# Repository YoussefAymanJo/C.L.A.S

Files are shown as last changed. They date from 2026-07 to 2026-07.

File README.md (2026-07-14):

# C.L.A.S

## Description
Is an abbreviation for a closed-loop feedback system.A system that monitors and acts based on lettuce & pepper plant conditions in 6th October city,Egypt.
In  monitors temperature & Humidty & soil moiture & light intensity.then,it responds in case in change in plants optimal range conditonns.As,it used actuctors,peltiers ,humidifier,heating lamp ,grow light , water pump and fan to out excessive humidty.It powered by esp s3.and cloud base storage of firebase,show data at moment on web app.
## Why it was built
This is grade 11 Capstone Project in my school,so i must make it.It is about the challenge Egypt faces in integrating IoT closed systems with farming.My project solve this by providing high nutrition needed crops in my area all the year,lettuce&pepper controlled  by closed feedback system.that control temperature & humidty & soil moisture & light parameters.
## How to use it / Build it
 First of all,prepare materials ,then buy wood and start cut into blocks,after that open parts in wood using cnc for actuactors and other in pcb enclosure.After that assemble all together using nails and wood glue.then adding electronic compontes sesnor & actucators.and connect them first to power supply to test it.then connect each one alone first to esp ,then test them all.after that,check wire isolation and system working and real data from sesnors.test system manul for 2 h. Finally, add plants and soil.
## Schematic
I made symbols & footprints for missing parts in kicad,then wires them ,and add pin headers instead of wire sensor direct to pcb,finally,organize schematic and adding flow diagram of system feedback.


## PCB
pcb consist of pinheaders and will connect to sensors using isolated wires & jumpers,and actuctors will connect to mosfets.I made pcb on kicad,body outline first,the routed componets together.


## CAD
i assembled greenhouse on fusion and make enclosure for pcb ,power supply & buck.



## Firmware
I made esp code and web to monitor data form firebase,but i will add js part later during building
### ESp code 

### website 
https://youssefaymanjo.github.io/WEb-clas/
## BOM 
I made the BOM  and needed materials ,in egypt then convert its price to USD dollar.


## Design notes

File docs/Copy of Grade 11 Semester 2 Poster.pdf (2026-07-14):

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
Aref | C.L.A.S Marwan Ahmed

# Youssef Ayman

10205
Abstract | Conclusions Grade 11 2025-2026

# 1st Semester STEM High School for Boys - 6th of October

# Introduction

Egypt struggles with some harsh challenges that hinders its development towards the vision of 2030. Through this vision, Egypt was facing tough problems that may stops the progress of the 2030 vision. One of these problems is the pollution of air, water, and soil, damaging the crops and the crop land. Egypt generates over 100 million tons of solid waste annually including Municipal solid waste, Construction and demolition waste,and Industrial and agricultural waste. Also, Egypt produces 16.4 billion cubic meters of wastewater annually including agricultural sources, and sewage. The health of the soil in the Nile Delta region is declining due to the growing number of enterprises and their emissions, urbanization, increased congestion, and the utilization of sewage and waste sediments. Although the Nile Delta covers only 20,000 km2, it accounts for 46% of Egypt’s total agricultural area, which is 55,040 km2

Image | Name | Quantity | Description
| Recycled wooden box | 1 box | A recycled wooden box to contain all the components in it.
| Polyethylene Film | ~ 2 meter-squared | A single layer film used to wrap the prototype to prevent heat leakage.
Relay module | 2 4-channel 1 2-channel

A module which turns on/off the actuators based on a signal from the ESP32.

ESP-32S 38Pin | 1 Dev board | The motherboard of the whole prototype, it is responsible for managing all the parts and the signals passing through.
Peltier | 2 Peltiers | Are devices responsible for generating heat flux by passing electric current to the both sides.
DC Fan | 5 Fans | Are significant for venetrating the prototype parts.
Growth Light | ~ 1 meter | Used to give light to the plant that is responsible for its growth.

Soil moisture and irrigation growth model
Soil moisture is an essential topic in green farming, as it indicates when the plants need to be watered. Studies indicate that soil temperature and moisture are strongly interconnected and directly influence plant root growth and water movement. Additionally, higher soil temperature increases evaporation, accelerating moisture loss. However, the soil moisture sensor does not give a true percentage from the beginning; it needs more calculations following Equation 2

# Literature Cited

Ventilation and roofing impacts on temperature
The greenhouse roof traps heat, increasing internal temperature. Ventilation reduces this heat by allowing air exchange between the inside and outside environments.
Learning Outcome | Concept | Content | Relation
CS.2.06 | 1 | User interface

Helps to understand how
to design and manage
System using App
interface
BI2.09 | 2 to 4 | Hormone Cycle | Helps us to understand how closed feedback system operates
ES.2.09 | 1 to 6 | Earth Cycle | Helps us to understand how closed feedback system operates
PH.2.09 | 1 to 6 | Circuit and charge and discharge | Helps us to understand how closed feedback system operates
PH.2.10 | 1 to 4 | Ac & Dc generator | Helps us to understand how closed feedback system operates
ME.2.05 | 1 | power | Helps us to understand how closed feedback system operates

Light intensity and photosynthesis efficiency
Light intensity is one of the essential factors controlling photosynthesis in a greenhouse. Solar radiation gives the energy required for converting carbon dioxide and water into glucose, directly affecting plant growth and productivity.
Studies indicate that photosynthetic activity is strongly dependent on incident radiation, especially in controlled environments such as greenhouses, where light availability can limit or enhance crop performance. The factors that affect light intensity are distance, following Equation 3.

I is the light intensity, p is the power of the light source, and d is the distance from the light source. As the plant was moved closer to the grow light by increasing the height, since the distance is squared in the law, the intensity increases quadratically. Increasing light intensity causes an increase in the photosynthesis rate of the plant, following Equation 4.

P(I) is the photosynthetic rate and P_max is the maximum photosynthetic rate k is the half-saturation constant; with this law, it can be concluded that at high light intensity (P)≈P_max

Added all the parts via schematic connection to ensure it is working correctly, as shown in Figure 3.

Implemented the circuit and the rest of the parts of the prototype like the lettuce plant, as shown in Figure 7.

Test Plan
Test plan The objective of this test plan is to evaluate
the validate the prototype and design requirements, focusing on two key aspects, design and mechanism. Parameters testing
The prototype must be able to measure at least 3 parameters properly, in this case, temperature, soil moisture, and humidity were included in our prototype as parameters.
accuracy
To ensure that the device has good accuracy, the temperature, soil moisture, and humidity are measured using the prototype from the STEM High School for Boys - 6 of October school to make sure it met the design requirements within the selected location.

th

Studies indicate that soil temperature and moisture are strongly interconnected and directly influence plant root growth and water movement (Xu Zhang et al., 2025). As soil temperature increases, the thermal energy within the soil rises, enhancing evaporation rates from the surface. At the same time, higher temperatures
stimulate root metabolic activity, increasing water uptake by
plants. As shown in Figure 13, the humidity data collection of
tshaeme greenhouse as it was between 50-52% and 90% as it used the fan and the roofing ventilation system in the first graph showing the temp by percentage The combined effect of increased evaporation and root absorption leads to a faster depletion of soil moisture, particularly in greenhouse environments where heat accumulation is significant. The ventilation system contained a 12V fan for ventilation, as decided following Equation 5.
Q is the total heat lost, and m is the airflow rate, and is the difference between T inside and T out. Indicating that the heat lost with the ventilation system depends on the strength of the fan used

This is critical for Lettuce and Capsicum annuum, since excessive heat can cause stress and reduce productivity. Moreover, the lettuce needs a temperature between 60 () which can be hard to maintain in the summer due to the temperature. The temperature affects the transpiration rate of the plant as well,following Equation 1.
As E is the transpiration rate of the plant and T is the temperature, in other words, the higher the temperature, the greater the loss of water in the plant that the system must maintain.

Calibrated the sensors used for the prototype to make sure it is accurate.

Figure4: Recycled wooden crate

Wrapped the body with a single layer of polyethylene to prevent the leakage of heat from the greenhouse, as shown in Figure 7.

# Acknowledgement

# Materials & Methods

# Results

# Analysis

# Recommendation

Closed | loop
a | GRICULTURAL SYSTEM.

Figure 14: Real-Life Location

# Keywords: Agriculture, lettuce, Feedback System, database

The previous challenges Cause bad consequences, the climate change and the rapid increase in the greenhouse gases in the atmosphere. The climate change occurs because of the burning of the fossil fuels like petroleum. In the last decades, It was observed that the carbon dioxide emissions
in Egypt increased to be 258.37 million ton annually as
shown in the Figure 1.
Two prior solutions were introduced to address the problem. The first was the automated scale aquaponic system, designed for serve the aquatic life by controlling the fish growth in a neutral environment conditions. Smart agricultural solution to autonmous greenhouse control was the second chosen prior solution. It is designed to control the quantity of air in the vaccum, light, and heat inside the prototype.
During the prototype development process, design requirements were chosen to ensure that the prototype would be effective, eco-friendly, safe, accurate, an precise. The chosen solution was a closed-loop agricultural system for suitable for planting lettuce and pepper. It was selected to be implemented in STEM High School for Boys – 6th of October as a location.

Solar Photovoltaic Panels Integration
A highly promising direction in the future development of the project is to integrate a solar photovoltaic panel with energy buffer units in the project to ensure energy continuity. A solar photovoltaic panel is a device that converts the sunlight into electric energy as shown in Figure 15, will be coupled with a buffer unit which acts as an energy storage that is settled between the solar panel and the site of the electrical load. When the panels collect the sunlight and convert it into current, this current will be used in

Figure 15: an image for the solar photo-voltaic cells

Real-Life Location
Boarding schools face multiple difficulties regarding funds. There has been a rapid increase in services and products, which makes it a necessity for schools to find an alternative. As shown in Figure 14, it is highly recommended to make a real-life application of the project in STEM High School for Boys – 6th of October as the location for the implementation of our device's application.
At present, our school depends on external suppliers and delivery
services which increase the costs on the school's financial
manager, increasing the funds that the school apply for. This adds
more pressure on it to cover all the students' demands during their learning journey. This solution will help the school to save on the delivery and ship the food that comes to the students every day by using the project to produce its own demand from fruits and vegetables without needing any shipping which cases a lot. Giving all the students their specified portions of food without any decrease in its amount.

Where θ is the soil moisture by percentage, and the R_dry is the reading of the sensor as the soil is fully dry and R_wet Is the reading when the soil is fully moist

with water, and R current is the reading of the sensor when the soil is in its current state.

Equation 2: Relation between energy and temperature

For Egypt's development towards the future, 2030 vision must be achieved by solving its grand challenges. In this project, two grand challenges was addressed and aimed to be solved, the pollution of air, water, an soil, and the low number of agricultural and industrial bases in Egypt. These grand challenges are aimed to be solved by Egypt to not hinder its economy and development. The project is designed to be implemented in STEM High School for Boys – 6th of October as a real life location as it will help in the problem of high cost of food due to the increase in the cost of the fuel by providing a local source of food for the students. Its simple design and mechanism, ability to be held by the user, and the ability to fit at any environment are from its pros. The project is composed of recycled wooden box as an external structure surrounded by a layer of polyethylene, a tray for holding the soil, lettuce plant, ESP32 as a brain for the circuit, power supply to feed the prototype with electricity, sensors for measuring the temperature, soil moisture, humidity, light intensity as parameters. The project met the design requirements as it contains recycled parts, composed of three parameters with their actuators to stabilize the surrounding environment.

Ten essential materials were used in constructing the prototype, As shown in Table 1 | Negative Results At first, we brought a stepdown converter to decrease the circiut’s voltage and increase the current, but we found that the stepdown was damaged before it was used. This made us took more time than expected to complete the circuit. Secondly, The power supply that was bought to operate the prototype was 12V and 10A. That was a problem because most of the parts in the circuit needed 7A or more, so this made a significant problem on how to operate all the part with the same power supply. To solve this problem, the components were distributed to the power supply’s pins of 10A each to fit all the components.

In conclusion, many grand challenges that hinders its development and its 2030 vision, two main challenges was aimed and addressed by the capstone project, the pollution of air, water, and soil, and the lack in the agricultural and industrial bases. This project aims to solve these problems by providing a solution which is the closed-loop agricultural system, controlling the environmental parameters to make the environmental condition stable. The prototype was build from recycled materials, except the electronic components. It was chosen to integrate the project in STEM High School for Boys – 6th of October as a real-life location, solving the problem of high budget for buying and delivering the food to the students by integrate the prototype in the school to produce its own food, saving its budget.

Methods
Made the 3D design using onshape CAD software to make sure the dimensions are accurate, as shown in Figure 2.

Collected a recycled wooden crate as a body for the prototype, and bought all the electronic parts to build the circuit, as shown in Figure 4.
Build the prototype body using some old wooden parts and the recycled wooden crate by cutting the wood into pieces then sticking them to make the roof of the greenhouse body, as shown in Figure 5.
Added the water container, tray, soil to the greenhouse body as a basic structure, as shown in Figure 6.

Followed the schematic and connected the circuits components correctly, making sure it will work properly.

Polycarbonate Implementation
It is also highly recommended to implement polycarbonate sheets instead of polyethylene single layer sheets as shown in Figure 16, as it will help in developing and improving the prototype efficiency. Polycarbonate is a high-performance, transparent thermoplastic known for its exceptional durability, light weight, and excellent optical clarity. These properties make it one of the
most widely used alternatives to glass in both architectural and
industrial applications. There are many differences between the
polycarbonate and polyethylene sheets, making it more favourable to be implemented in the real-life project, such as High impact resistance, Superior thermal insulation, Excellent light transmission, Built-in UV protection, Long lifespan (10–25 years), and Reduces energy and heating costs. It is not implemented in our prototype because, it costs more than expected to fund it.

Ritchie, H., & Rosado, P. (2025, December 19). CO₂ and Greenhouse Gas Emissions. Our World in Data. https://ourworldindata.org/profile/co2/egypt

Figure 1: CO₂ and Greenhouse Gas Emissions

Figure3: Schematic connections for the prototype using kicad

Figure 7: Greeenhouse prototype after circuit implementation and polyethylene wrapping

Figure 6: Greeenhouse prototype after circuit implementation

Figure 5: Greeenhouse prototype after circuit implementation

Figure 16: an image for the polycarbonate sheets

Figure 13: greenhouse humidity data collection

Temperature effects on the greenhouse
Temperature is a key factor affecting plant growth, evaporation, and transpiration. In greenhouse systems, solar radiation enters through the transparent covering and is partially trapped, increasing the internal temperature. Research shows that evapotranspiration is one of the most crucial processes controlling water movement in greenhouse crops. As temperature increases, the kinetic energy of water molecules and plant physiological activity also increases, leading to higher transpiration rates and accelerated water loss from .

Figure2: 3D design for the prototype the root zone This process is further intensified by increased vapor pressure deficit between the leaf surface and the surrounding air, which enhances the diffusion of water vapor from the plant o the atmosphere. As shown in Figure 12, the data collection of the air temperature from the same study mentioned before. The data shows the air temperature over two months, with fractures as the temperature decreases at night and increases during the day, with an average of 22.5 .(Sustain. Food Syst,2023).

Figure 12: Greenhouse body after adding tray, and cooling system

Positive Results
A reliable closed-loop agricultural system was developed for use in STEM High School for Boys - 6 of October, conforming to the required design requirement, showing the responses from the actuators to the changes in the environment of the project relative to the time taken, and another one showing the environmental parameters changing by passing time.

th

Table3: Learning outcomes used

Equation 3: Relation between light intensity and distance from the light source Equation 4: Relation between photosynthesis rate and light intensity Equation 5: Relation between total heat lost and the air flow rate

Boulard, T., & Wang, S. (2000a). Greenhouse crop transpiration simulation from external climate conditions. Agricultural and Forest Meteorology, 100(1), 25–34. https://doi.org/10.1016/s0168-1923(99)00082-9
Ghiat, I., Govindan, R., & Al-Ansari, T. (2023). Evaluation of evapotranspiration models for cucumbers grown under CO2 enriched and HVAC driven greenhouses: A step towards precision
irrigation | in | hyper-arid | regions. | Frontiers | in | Sustainable | Food | Systems, | 7.
https://doi.org/10.3389/fsufs.2023.1155443
hort. (n.d.). https://journals.ashs.org/view/journals/horttech/35/6/article-p972.xml

Without Allah’s assistance, this work wouldn’t have been completed. Appreciating the great efforts of Ms. ninette refaat and her great role in supervising the capstone projects, our capstone leader, Mr. Mohamed Bekheet, our capstone general, Mrs.Mona, for their great effort in helping us in our project.

Figure 8: Graph for the reading of the light intinsity over time | Figure 9: Graph for the reading of the temperature over time Figure 10: Graph for the reading of the soil moisture over time | Figure 11: Graph for the reading of the humidity over time
Component | Current (A) | Power (W)
2x Peltiers | 10 | 120
Heating Lamp | 4 | 48
Grow Light | 1.5 | 18
Water Pump | 0.6 | 7.2
5x Fans & Humidifier | 0.86 | 10.4
Sensors | 0.01 | 0.1
TOTAL PEAK | 16.97 A | 203.7 W

Table 2: power consumption table

Equation 1: Relation between energy and temperature

the prototype during it is working, while the excess electricity will be stored in the buffer for future using during night or cloudy weather, helping in increasing the project efficiency, and using a source of renewable energy which is the sunlight. This makes sure that the prototype will be working with no obstacles in energy. However, it is not implemented due to difficulties regarding its high initial cost.

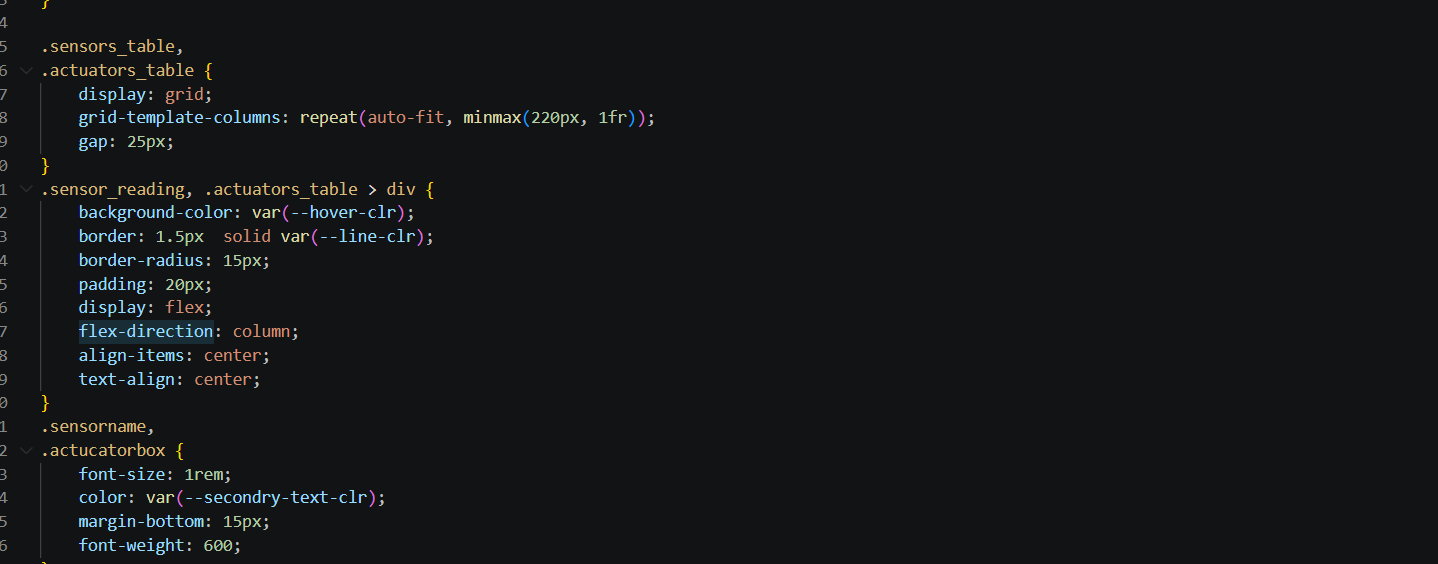
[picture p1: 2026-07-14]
Images/Screenshot 2026-07-15 015619.png

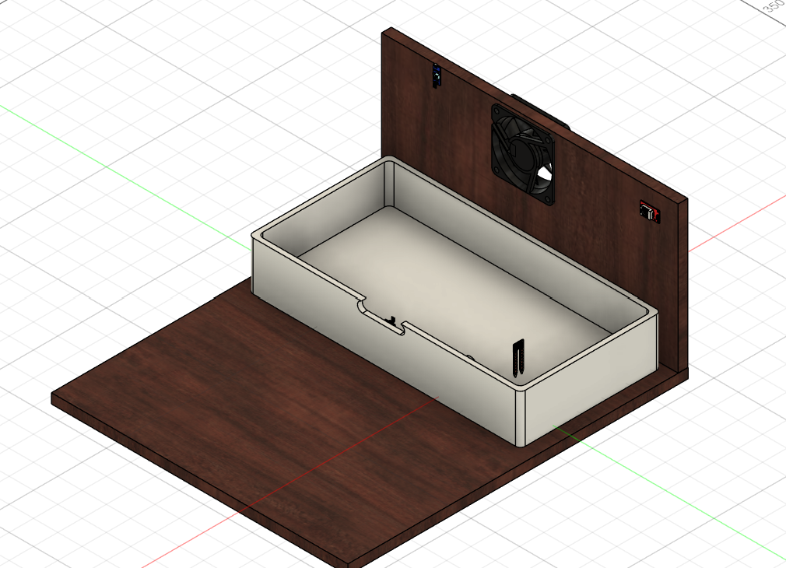
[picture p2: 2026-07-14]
Images/Screenshot 2026-07-14 233705.png

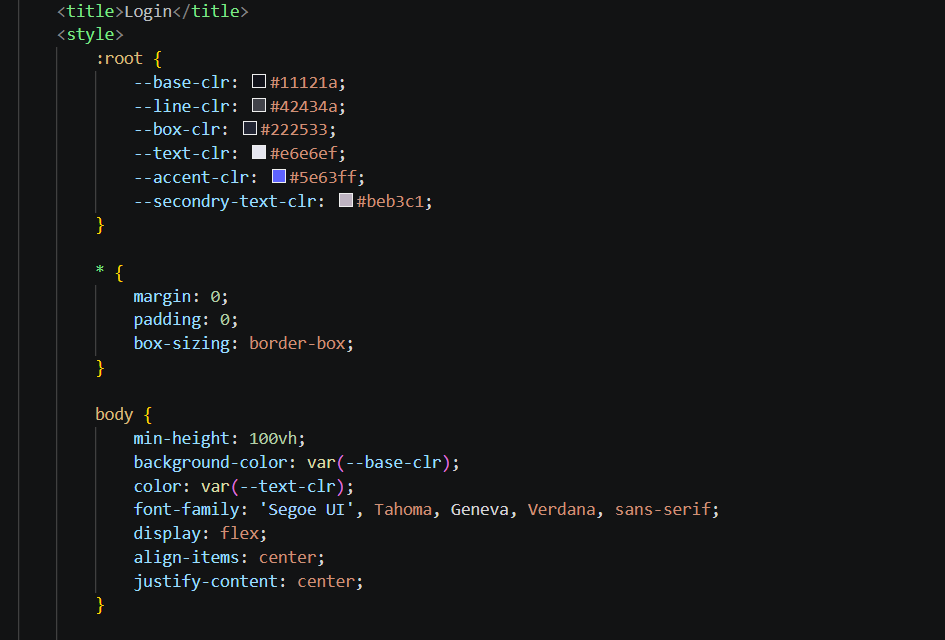
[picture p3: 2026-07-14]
Images/Screenshot 2026-07-15 012253.png

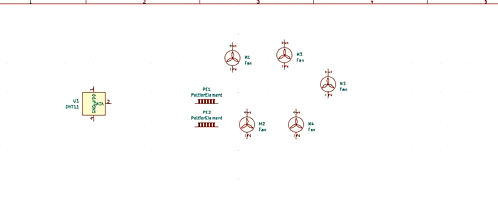
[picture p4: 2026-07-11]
Images/Screenshot 2026-07-08 211201.png

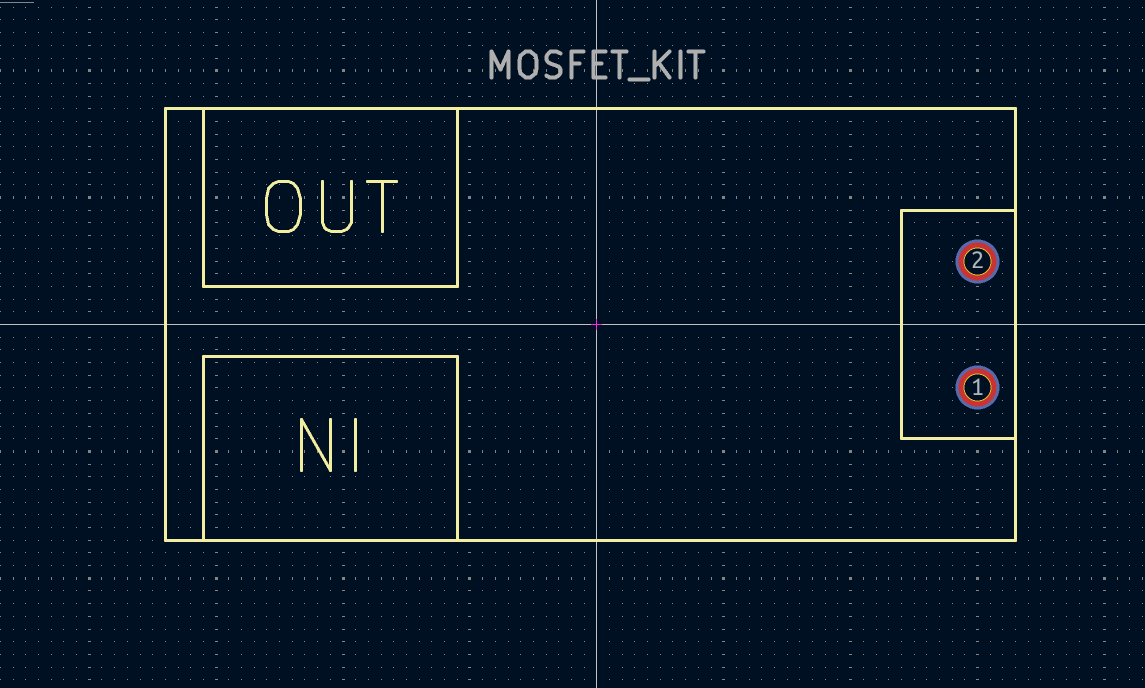
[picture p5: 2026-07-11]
Images/Screenshot 2026-07-09 143521.png

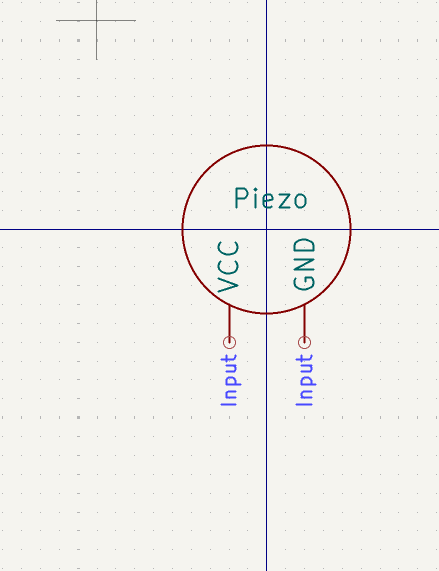
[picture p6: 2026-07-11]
Images/Screenshot 2026-07-09 143455.png

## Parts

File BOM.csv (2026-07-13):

Item | Descritption | Qt | link | price
DHT22 | Measure temperature & humidty | 1 | https://makerselectronics.com/product/dht22-digital-temperature-and-humidi/ | 3
LDR | Measure ligth intensity | 1 | https://www.ram-e-shop.com/ar/shop/kit-ky018-ldr-ldr-module-4pin-photoresistor-sku-ky018-7075?category=180 | 0.7
Soil Moisture | Measures Amount of water in soil | 1 | https://www.ram-e-shop.com/ar/shop/sen-soil-a-soil-moisture-sensor-sku-soil-a-7058 | 1
Water level sensor | Measures water level | 1 | https://www.ram-e-shop.com/ar/shop/kit-c43-water-sensor-c43-water-level-sensor-liquid-water-droplet-depth-detection-7157 | 0.5
Mosfet kit 400w | Controlls on/off actucators | 7 | https://www.ebay.com/itm/147073435080 | 24
Power supply 20a | Provide power for system | 1 | https://microohm-eg.com/power-supply-smps-12v-20a-with-fan/ | 6.42
step down | reduce power to 5v | 1 | https://www.ram-e-shop.com/ar/shop/dc-dc-101-dc-dc-step-down-converter-adjustable-5a-xl4015-5v-32vdc-to-0-8v-30vdc-sku-dc101-bwrd-dyr-khfd-jhd-fwlt-7258 | 2
Peltier | cool down greenhouse | 2 | https://www.ram-e-shop.com/ar/shop/sf10080-thermoelectric-cooler-40x40mm-peltier-6726 | 7.02
Peltier Kit | Sperate peltier air throw vacuum | 2 | https://microohm-eg.com/thermoelectric-peltier-refrigeration-cooling-system-80x80x80mm-for-tec1-12706/ | 13.64
Fan 12 v 50*50 | cool down petlier heat side | 2 | https://www.ram-e-shop.com/ar/shop/fan-12vdc-5010-cooling-fan-12vdc-size-50x50x10mm-mrwh-tbryd-12-fwlt-6636 | 1.81
Fan 12 v 120*120 | reduce Humidty | 1 | https://makerselectronics.com/product/dc-fan-12v-0-35a-120x120x38mm/ | 3.21
Humidifier | Increase Humidty | 1 | https://lampatronics.com/product/usb-mini-humidifier-mist-maker-and-driver-circuit-board-fogger-atomization-full-kit | 2.41
Water pump | Water plant | 1 | https://mostelectronic.com/shop/air-fluid-control/ultra-quiet-brushless-dc-water-pump-12vdc-3-6w-240l-h-ip68/ | 5.52
Water Pump - Hose 6x8mm - PVC Clear Vinyl Tubing 1 Meter ????? ???? ??? 1? | Delivel water to soil | 2 | https://www.ram-e-shop.com/ar/shop/dc-pump-hose-6x8-1m-water-pump-hose-6x8mm-pvc-clear-vinyl-tubing-1-meter-khrtwm-mdkh-twl-1m-7954 | 1.4
Heating Lamp | Increase heat in greenhouse | 1 | https://www.amazon.eg/-/en/Incandescent-Infrared-R125-Spotlight-Bathroom/dp/B0D1W4ZKD4 | 10.41
Grow LIght | Alternative of sunglight absence | 1 | https://www.amazon.eg/-/en/Waterproof-Spectrum-Hydroponics-Greenhouse-Gardening/dp/B0DPT5ZH7L | 13.84
Esp S3 | MCU of circuit | 1 | https://store.fut-electronics.com/products/esp32-s3-devkitc-1 | 11.03
Pin headers | For PCB | 1 | https://www.ram-e-shop.com/ar/shop/ph10-1x40-male-ph10-pin-header-male-1x40-straight-2-54mm-long-leg-17mm-5832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 | 0.08
M3 5mm | Hold PCb | 6 | https://microohm-eg.com/screw-m3-3mm-x-5mm-without-nut/ | 0.08
Screw terminal | 5v in for PCB | 1 | https://www.ram-e-shop.com/ar/shop/r-5-roseta-2pin-2-pin-pcb-screw-terminal-block-pitch-5mm-14-1mm-height-r-5-6323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 | 0.08
Tray | Hold soil | 1 | https://plantifyshop.com/en/product/microgreens-germination-tray/ | 1.64
Jumpers | Male to female | 1 | https://www.ram-e-shop.com/ar/shop/ph60-mf-20cm-ph60-20cm-male-to-female-40-jumper-wires-set-7066 | 0.7
Panel Mount AC Power Male Socket | Control power in | 1 | https://makerselectronics.com/product/panel-mount-ac-power-male-socket-2/ | 0.7
Copper wire | Wire | 4 | https://www.amazon.eg/-/en/Electrical-Power-Cable-Copper-Speaker/dp/B0C4BTR7CG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 | 4.25
Nails | Nails | none | none | 1
PCB | PCb printing | 1 | None | 50
Wood | Wood | none | none | 20.06

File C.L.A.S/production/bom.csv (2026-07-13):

Designator | Footprint | Quantity | Value | LCSC Part #
FAN1, HEATLAMP1, HUMIDIFER1, PELTIER1, PELTIER2, WATERPUMP1, WATERPUMP2 | MOSFET_KIT | 7 | ~
J1 | TerminalBlock_Phoenix_MKDS-1,5-2-5.08_1x02_P5.08mm_Horizontal | 1 | Screw_Terminal_01x02
J2, J3, J4, J5 | PinHeader_1x03_P2.54mm_Vertical | 4 | Conn_01x03_Pin
U1 | XCVR_ESP32-S3-DEVKITC-1-N8R2 | 1 | ESP32-S3-DEVKITC-1-N8R2

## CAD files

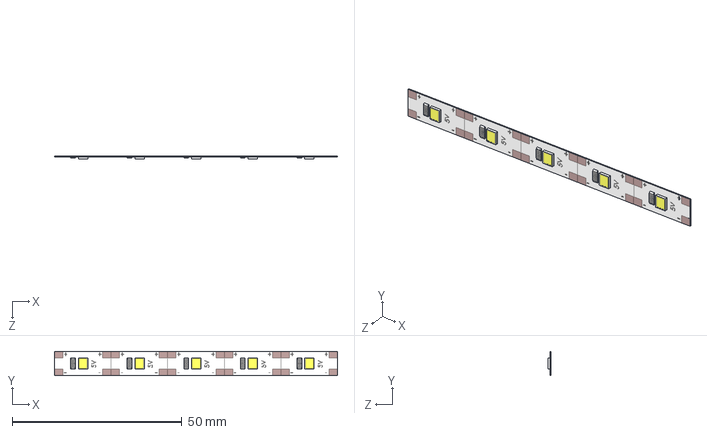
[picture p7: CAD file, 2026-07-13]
Production/LED_5V_5x.STEP
83.4 x 7.20 x 1.00 mm
LED_Segment5V_60 x 5

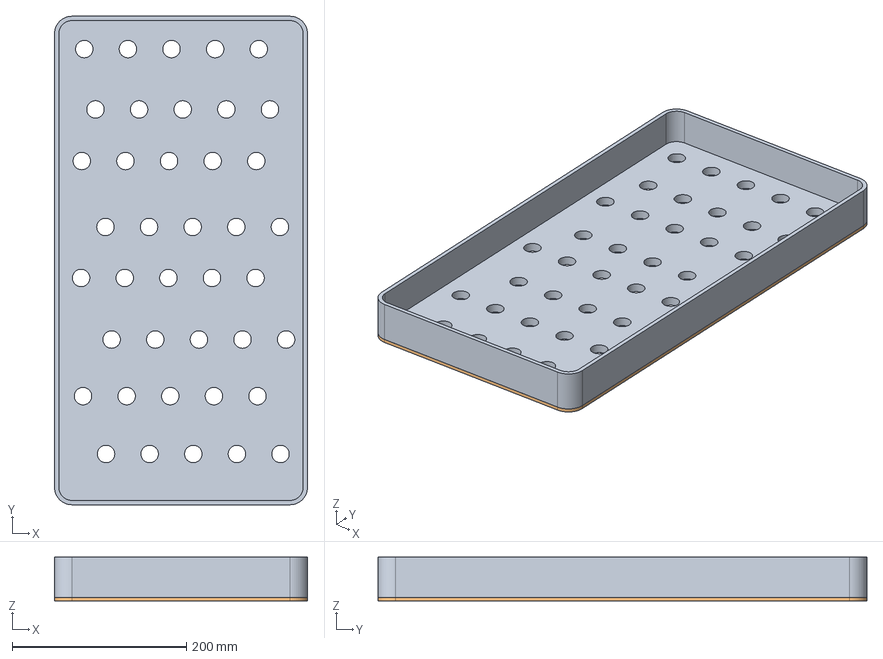
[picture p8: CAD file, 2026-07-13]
CAD/Trey.step
290.0 x 560.0 x 50.0 mm

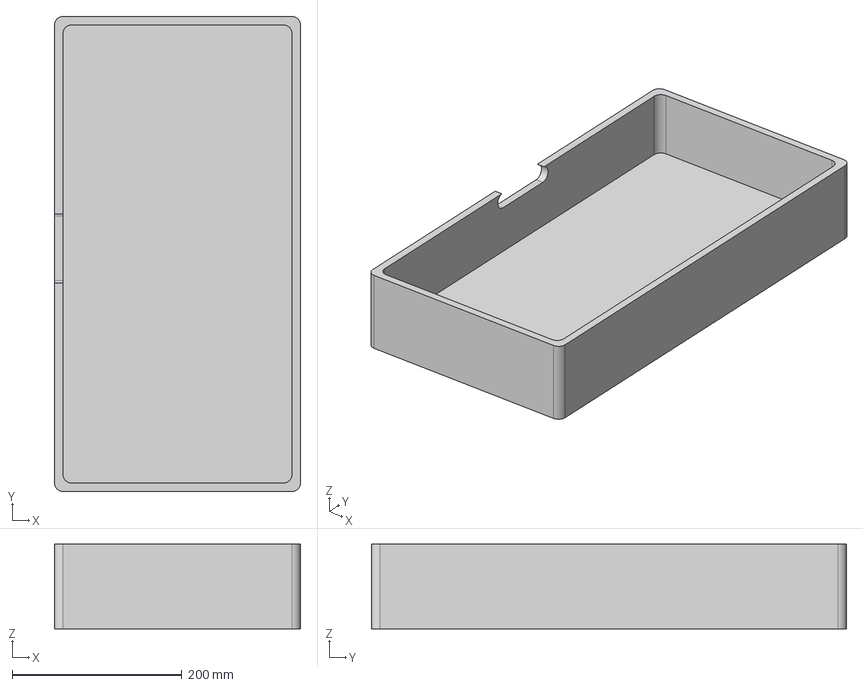
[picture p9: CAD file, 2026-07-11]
Production/waterbox.step
290.0 x 560.0 x 100.0 mm

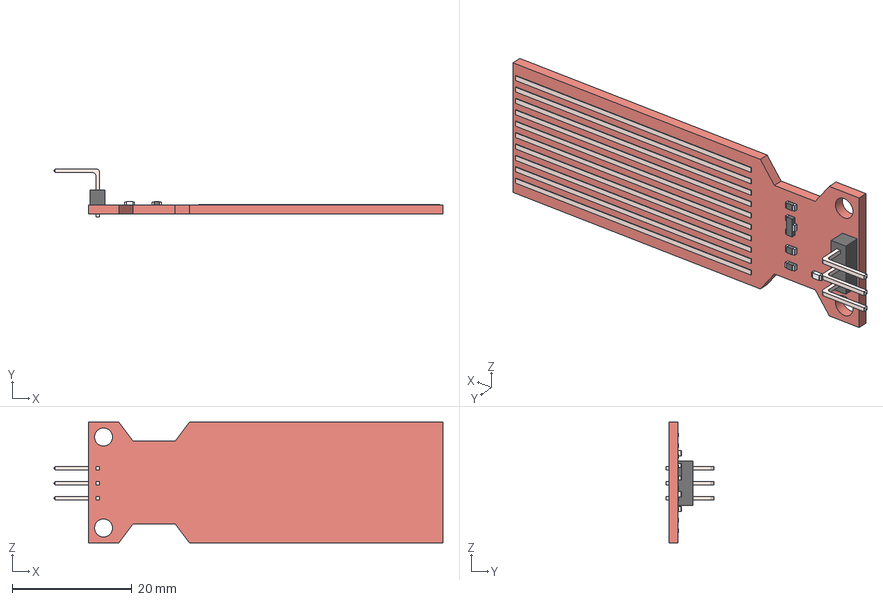
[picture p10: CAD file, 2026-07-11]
Production/Capteur Pluie2 v3.step
65.0 x 8.00 x 20.2 mm

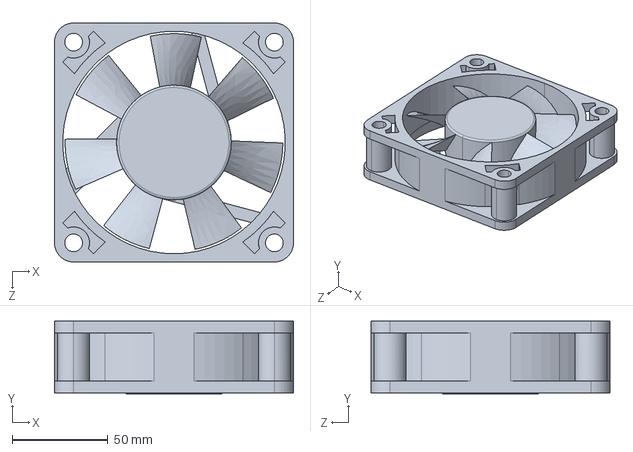
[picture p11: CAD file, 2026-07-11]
Production/24V DC cooling fan.STEP
125.0 x 38.0 x 125.0 mm

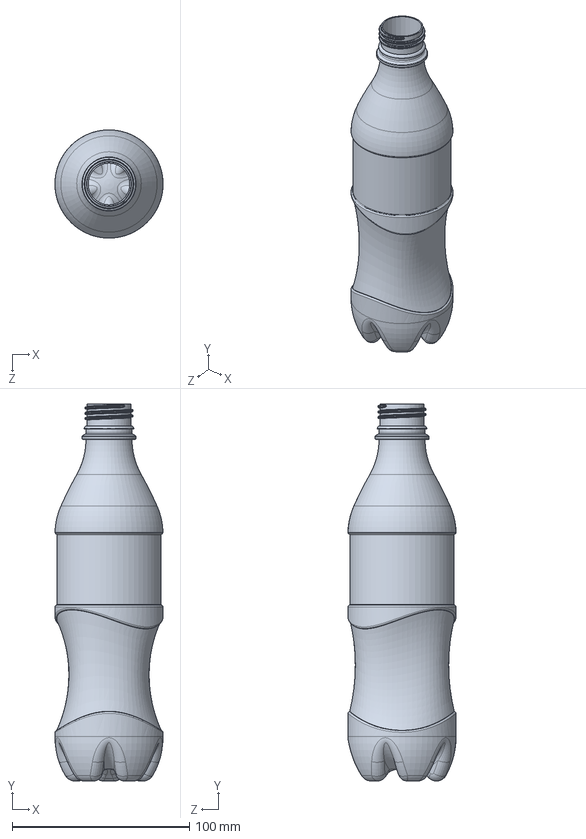
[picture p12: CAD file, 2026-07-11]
Production/Water Bottle.SLDPRT
61.0 x 212.5 x 61.0 mm

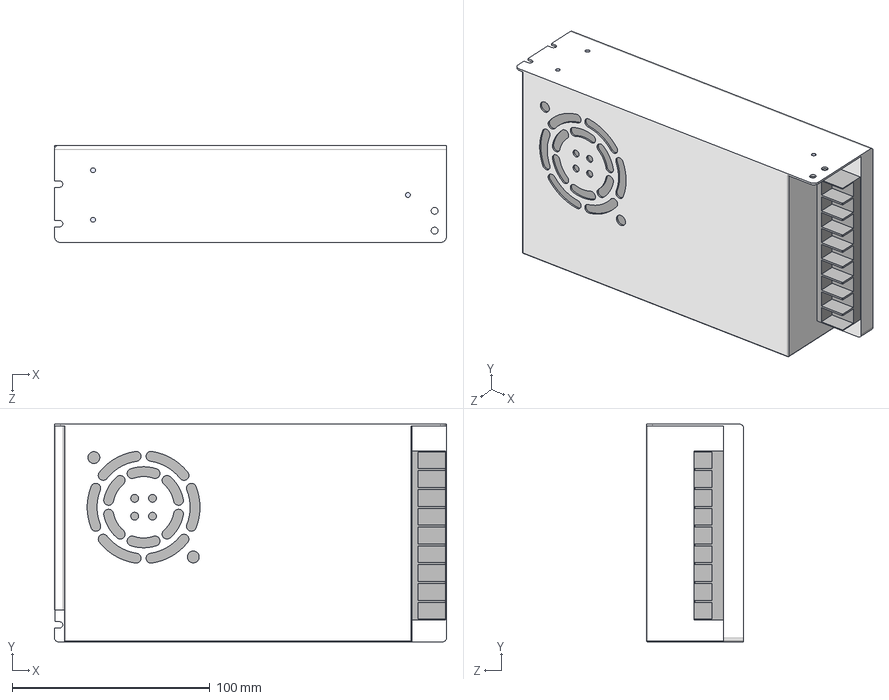
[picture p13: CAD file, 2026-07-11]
Production/Power supply 12V 20A.STEP
198.0 x 110.0 x 49.0 mm

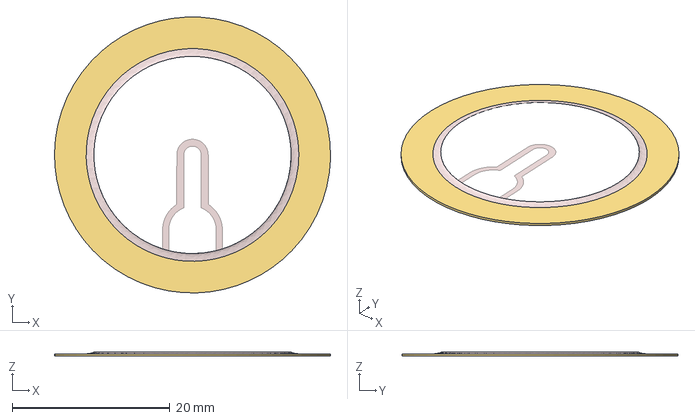
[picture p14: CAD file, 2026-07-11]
Production/Piezo Element, Self Oscillating Type.stp
35.0 x 35.0 x 0.56 mm

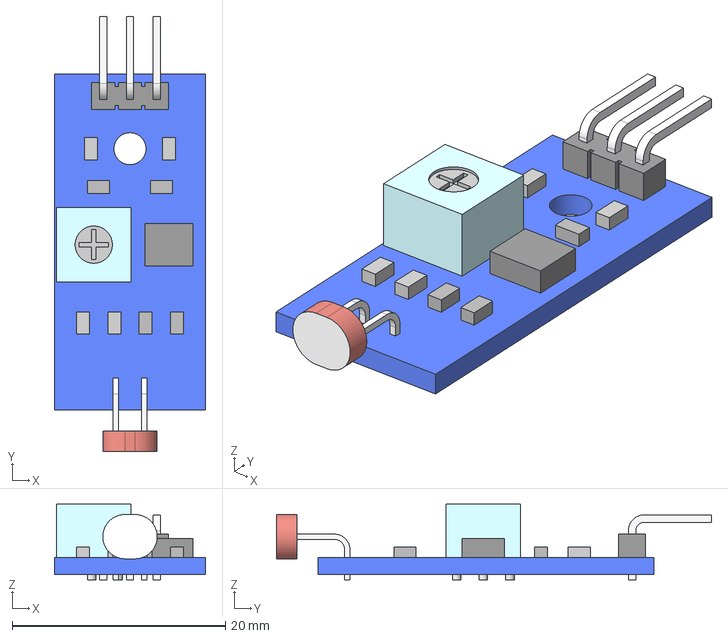
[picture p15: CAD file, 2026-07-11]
Production/Light sensor LDR v1.step
14.2 x 40.8 x 7.10 mm

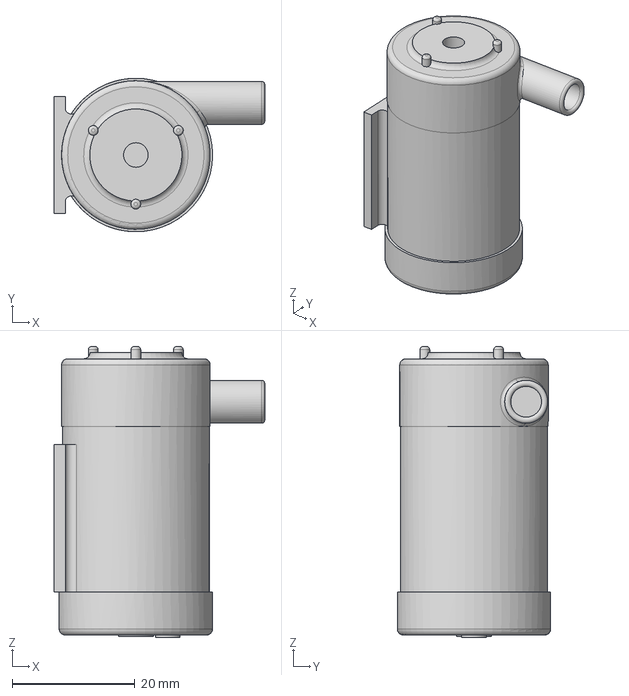
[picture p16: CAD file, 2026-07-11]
Production/Pump.step
34.3 x 25.0 x 47.4 mm

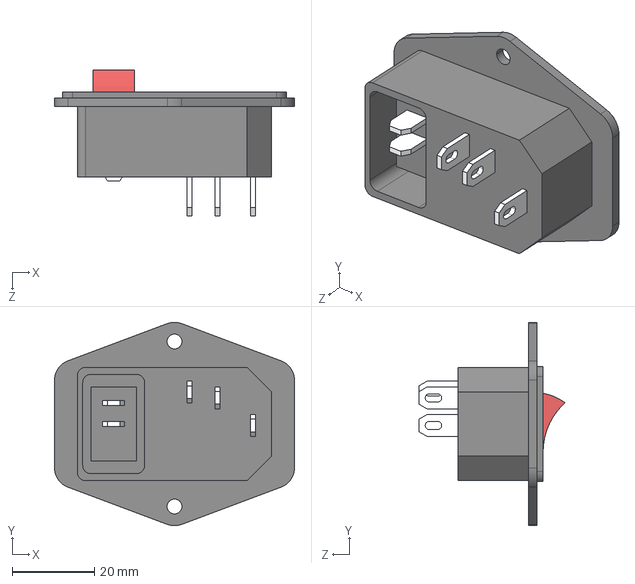
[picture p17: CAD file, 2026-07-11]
Production/power connector.STEP
58.2 x 49.3 x 35.4 mm

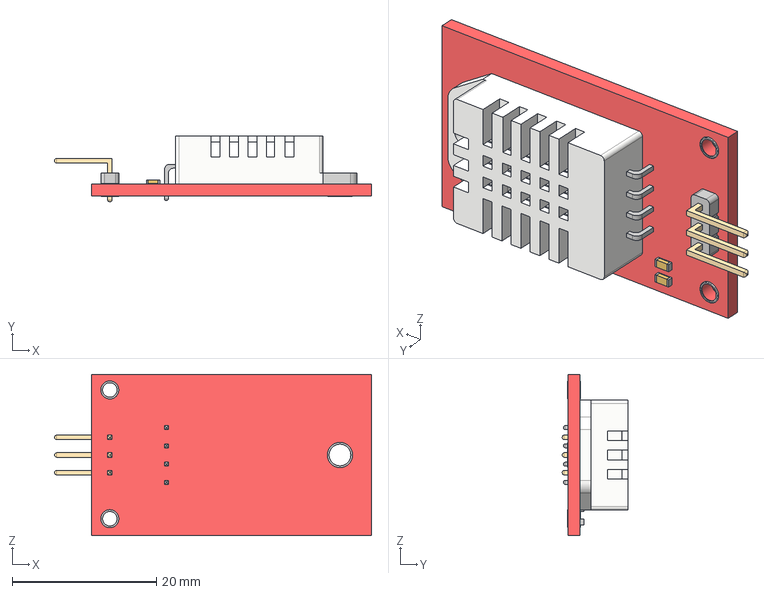
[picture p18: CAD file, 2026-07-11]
Production/AM2302 v1.step
43.9 x 9.08 x 22.3 mm

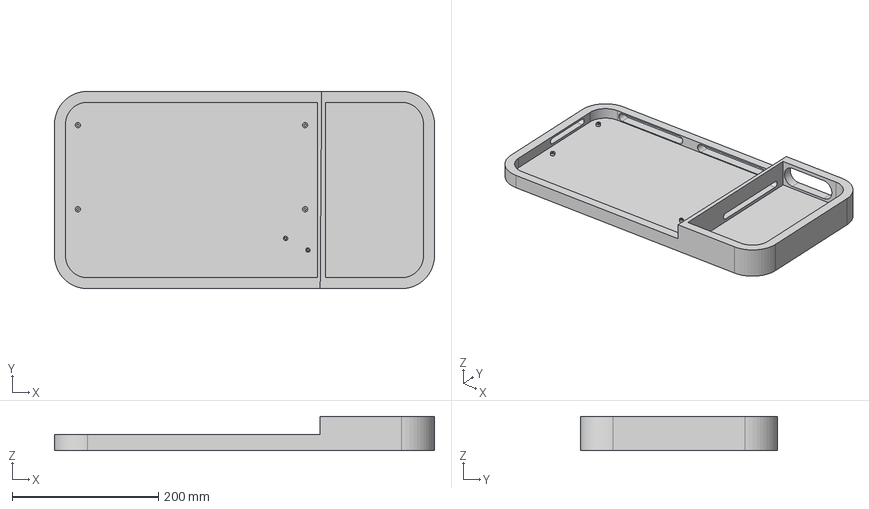
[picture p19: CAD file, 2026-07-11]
Production/Enclosure.step
520.0 x 270.0 x 47.0 mm

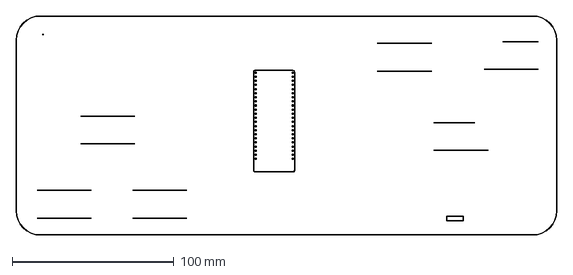
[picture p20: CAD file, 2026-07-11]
Production/Sketch_PCB.dxf
334.5 x 135.5 mm

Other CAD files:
Production/Soil-Moisture-Sensor-Probe.stp
CAD/M3x5 SHCS v1.step
CAD/M3x5 SHCS v1.f3d
CAD/Trey.f3d
Production/bulb.f3d
Production/waterbox.f3d

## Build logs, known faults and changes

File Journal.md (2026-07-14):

author: Youssef Ayman Mohamed

 description: Closed feedback greenhouse system for lettuce and pepper plants in Egypt. Controlled by ESP.
 
 created_at: "2026-07-3"

## Entry 1 
created at:2026-7-3

### Content 
During this session, I  workedmainly onon searching and sketch down worflow and used materials. Firstly, I used the draw.io app to sketch class materials. Firstly,  I started by adding the MCU, which is esp s3, then I went to sensors, which are DHT22 & ldr, and soil moisture. After that,  I added actuators for each parameter: 2 Peltier cooling kits for high temp and a vice versa heat lamp for low temp. Then, for humidity, I added a humidifier piezo for low humidity and a fan to release air when it increases.
Then,  a water pump for watering when moisture decreases and a grow light in case of absence of sunlight.

After that, I added a power source. I used a 20A power supply after calculating the usage of each part and used a step-down to 5V to 5v provide power for the ESP and sensors.  Then, the firmware will be a tkinter app and firebase as feedback for the user. Finally, I worked in schematics adding symbols available on KiCad, such as Peltier & ESP & fan.



### Recording (46 min) :

https://lapse.hackclub.com/timelapse/fNMql2ZkObp6

## Entry 2
created at:2026-7-5

### Content 
During this session, I worked mainly on the schematic.
Firstly, some parts do not have their symbol in KiCad or even on SnapMagic. So I watched a tutorial on creating symbols in KiCad.
After that, I started making a soil moisture sensor symbol and found out its pinout. I faced some struggles as it was  my first one.
Then,ldr sensor, after searching about its pinout.
Then, I made power parts, which are a buck converter and a power supply, in the same way.






Then, I made a humidifier symbol, as it is primarily piezo. After that, I started wires componets togehter with ESP,a nd organized a bit on the schematic, as sensors, and actuators in different boxes. I wired all sensors to the main GND for the buck. But I found esp s3  symbol & footprint on kicad was have issues, so I downloaded another one from SnapMagic and imported it into KiCad.



Secondly,working on power controllers,mosfet kit with 2 mosfet and  operate upt to 400w ,was suitable,as it small and faster than relay.I searched on footprint for it alot but nothing founded,so i made first it sybmol,based on its dimensions and it pinout,after,i made it footprint.I searched first for its 3d model,and found it on grabcad.then watching video to made footprint.Finally,i made the footpring based on it dimensions,then attach 3d model,and align pad opening with opens in 3d model.



thirdly,i worked on esp s3 model,attaching it,then i started adding pin headers for sensors and screw pin for power.then wires them with esp and add their footprint.After that,i worked on power controlles,i found first that pins in symbols not sync with footprint,after several tries,founding errors in numbering of pins in symbol and footprint.after that i started wire power controllers for each aquctors.


Finaly,i worked description of clas.then making worflow for each parts in system and the process in firmware will be.


### Recording (4.4 hours) :
https://lapse.hackclub.com/timelapse/867AXAJ3zznD
https://lapse.hackclub.com/timelapse/h2mKk20hOjvF

## Entry 3
created at:2026-7-8

### Content 
During this session, I worked on PCB
Firstly,i add edge cuts forming pcb shape,then i organized componets inside it,cosider the wires.then i started routed pcb,routing mosfets and pin headers with esp32 s3.Then,i create copper area on the top for VCC 5 v and on the back another one for GND.then cehecking drc,after that i added function for each part above it,and sign my name on pcb.




### Recording (29 min) :
https://lapse.hackclub.com/timelapse/yJk0d57BnSbP

## Entry 4
created at:2026-7-9

### Content 
During this session,i worked mainly on pcb enclosure.
firstly,i uploaded pcb  3d model to fusion,then sketck it dimensions,then worked on enclosure sketch ,adding offset and taking parts for m3 screws,
After that,i added mouniting holes in schematic,then assign it footprint.
then,i searched for componetes 3d models on grapcad , power supply,buck ,sensors and actuators.


after that i added water level sensor,i searched for its pinout,then making it symbol in kicad, then,update schematic and adding 3 pin headers for sensors,after that update pcb and reroute new headers.then upload pcb model to fusion,but mosfets 3d were absent.So i added them manually.
Then,i assembles pcb & power supply and buck and align them ,then project them to new sketch.then extrude enclosure  by heigth of power supply.then extrude base .after that, sketch mouting holes for m3 screws 5mm.then extrude it.




Secondly,I assembled enclosure with parts to check openiin places according to mosfet and power supply.then started sketch  slots on the back and left of enclosure.then cutted it.After that,i searched for ac panel plug 3d model,then uploaded it to enclosure beside power supply.then extrude openinig for it.
After that,i worked on pcb cover,sketched it and extrude it.then i added project text on the top.And tried to add lettuce image but doens't work.then i added it to assembly,then adding m3 5mm srews for pcb and buck and used surface anaylsis for top and right.

Finally, I rendered the enclosure with white to reflect sunlight without increase pcb temperature.



### Recording (3 hours & 15 min) :
https://lapse.hackclub.com/timelapse/dNaEws2EPQLG

https://lapse.hackclub.com/timelapse/mTek28ENGT2j

## Entry 5
created at:2026-7-11
### Content 
During this session,i worked mainly on greenhouse assembly.
I started measuring componets dimensions,such as peltier kit and tray.then i started sketch plant tray based on it online dimesions.after that ,i added holes in it and repeated theam accros tray.then extrude it by 4 cm .

Secondly,i was not had any idea to make greenhouse for first time,so i decided to make it from blocks and assemble them together like lego.at first,i make base block,and it should hold pcb enclosure & tray and humidty bottle.after edited its dimesions for them,i uploaded piezo element for humidifier above plastic bottle.t
After that,i searched for fridge box for watering water align witg tray.founding one on amazon.then i started extrude water box.and assemble it with below tray.
then,i cut slot in the middle for water level sensor.and added it.then adding soil moisture sensor in the tray as soil in.

thirdly,i make second block.and added it for greenhouse,then uploaded dc fan responsible for reduce humidty.then cut poloygn in block for fan.and added dht 22 & ldr sensors,and cut hole for it mounting holes so the sensor will be attached by srews.
After that,i made the left and right block,then extrude opening for 2 peltiers kit on each one.

Finally,i searched for greenhouse roof types.and fount A frame is suitable  egypt coditions and my challenge.then, four wood plate will hold polyethanael layer that cover greenhouse,and assemled them adjusting angles to fit on each other.
after that,i rendered greenhouse,tray & blocks.then i found way to add poly appearce by adding more lego blocks,then make them glass appeareance.
so i made roof on 2 blocks & left block,then making triangle to cover parts between roof and side blocks.
then,i renderd greenhouse assembly.


### Recording (2 h & 44 min) :
https://lapse.hackclub.com/timelapse/jrJTmdQnPTF2

## Entry 6
created at:2026-7-12
### Content 
Firstly,grow light power control mosfer was missiing,so i added it to schematic and connect it to 5v,then i uploaded pcb and rerouted new mosfet.then export new 3d model and also export gerbers folder.


After that,i added mosfets 3d model to pcb, then upated pcb in it enclosure,and realign it with screws using surface analysis.then update greenhouse assembly.
then,i seacrhed for grow light strip 3d model,and trying to add it on sides cover,but i will not cover all crops.so i put them on top wood A roof.adjusting them to be connected.then i rendered the layers of polyehtanel to make it more clear by glass appeareacne.

Secondly,i worked on BOM file,adding item name and link in shop and their price in usd.

Finally,i searched for dashboard UI and found some cool UI ,gaining ideas for my dashboard.


### Recording (1 h & 47 min) :
https://lapse.hackclub.com/timelapse/XfLlIYKGBLIV

https://lapse.hackclub.com/timelapse/Oo2w71q-Nlll
## Entry 7
created at:2026-7-12
### Content 
During this session I worked mainly on Esp code.
firstly,i imported dht22 sensor library.then defined pin for sensors dht22 & ldr & soil moiture and water level.after that i defined pins for actucators power controllers.
then,i create struct for lettuce and pepper conditions ranges based on my 4 paramters.then,define pins as input and read sensors readings,convert water level readings to usable value by equation.

after that,i created 3 if cases ,first one for lettuce coditions ,2 for pepper and last one for manual operating by user for testing or overide.i sperated cases for each parameter into 3 ,first on ,if it below the range , above range and between range.for instance,if temp below range heat lamp on and otherwise peltier on ,if on range all off.
Then,i imported firebase client libray and wifi library for esp,then define wifi & password and firebase url and sercet code.
then,added wifi connection server in setup function,and loop until it connected in while loop.
then,i call planttype from firebase and store it,then it will determine case 0 for lettuce,1 pepper and left for manual.in each case,i define bool variable 0 for  on and 1 for off and change them  based on case.




finally,in third case ,i get actuctors status from firebase ,then print it in serial monitor.then upated firebase with sensor readings every 30sec and actuctors status.



### time (2 h & 5 min) :

## Entry 8
created at:2026-7-14
### Content 
During this session,i worked on dashboard.firstly,i want to make sidebar for navigation,so i watched tutorial how to make one,then i made it ,it consist of Home,about us and logout.i made main nav contianer then first div for projec name and logo on top  and icon form google icons,then unodered list for navigation elements,each one consist of link for another page and icon and span for title and reconized active page with active name class.and at end div for logout.


about css for nav bar,sidebar box properties from size ,height ,bg colour and align ,then active highlight ,then logos and text css and hover animation bg colour.then title css from font family & size & colour and disply,finally,logout css.




After that,i made simple dasboard ui without js,i will add it when buidlnig and testing clas.firstly,i make grid of boxes show guage contianer of sensors readings and same grid of boxes for actuactors on/off.then css for dashboard,firstly i made css for boxes form size and colours and align items.after that,i make guage css,then css for button in actuactors boxes,later i will add js with firebase for them but i need prototype and recieve real readings from sesnors.







### time (3 h & 2 min) :

## Entry 9
created at:2026-7-14
### Content 
During this session, I worked on the login and about pages.
firstly,in about us page,i coped navbar code form home page and edited it to be active on about us.i want to show my project scientific poster in this page for school evaulators,so i used iframe element in html and uploaded pdf.first,edit on main contianer properties ,alig element at center,adding padding from top and bottom ,
then i added css for h1 element to be in center with specific colour from my plattet,with weight 700 and size 2 rem.then align ifram in center with 100 width and height and border raduis 0.75em.




Secondly,login Page:i watched some tutorial to make simple login page,i will add later js in testing prototoype,but now just ui.
i made first main div for lonig box and added div for title and 2 field divs for username and password.then a href link for index page.
then i started css in html , i use same colour variable form index.then  first make body properites,bg colour and elements aligment in center.then i made login box,with 300px width and border 2px ,bg colour.after that, align h1 name in center , then  divs fields for username and password  css.finaly,i tried to make a href look like button.



### time (53 min) :

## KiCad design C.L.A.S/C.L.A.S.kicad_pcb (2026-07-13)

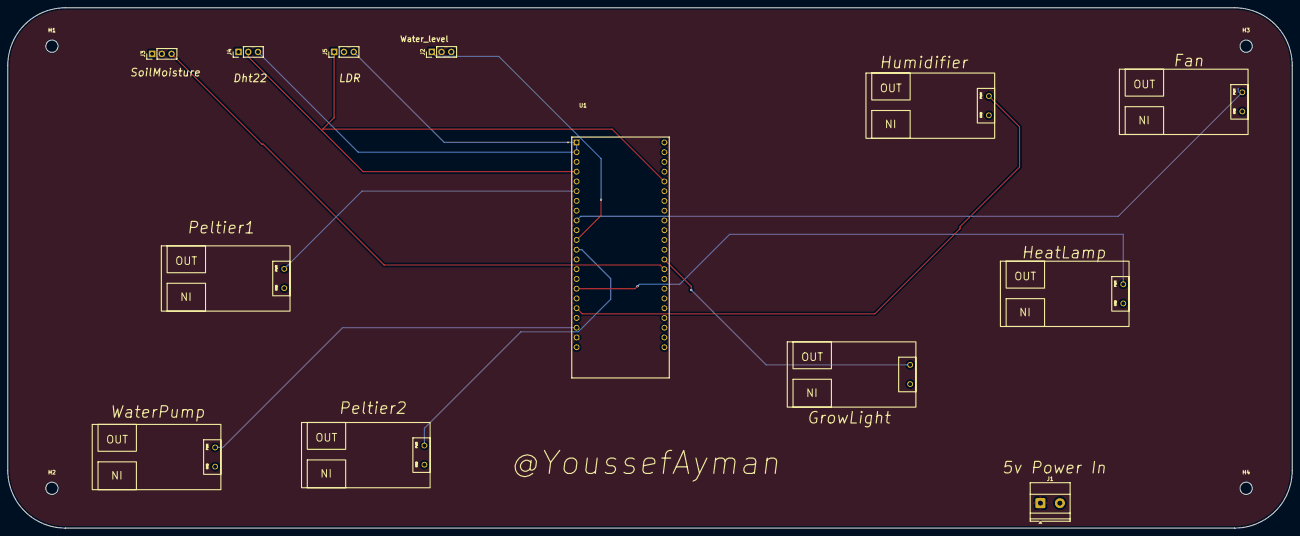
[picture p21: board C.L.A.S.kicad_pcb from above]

Board: 2 copper layers, 334.5 x 135.5 mm, 17 parts (0 on the bottom side), 14 nets.

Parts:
Fan1: MOSFET_KIT
H1, H2, H3, H4: MountingHole; MountingHole_3.2mm_M3
Heatlamp1: MOSFET_KIT
Humidifer1: MOSFET_KIT
J1: Screw_Terminal_01x02; TerminalBlock_Phoenix_MKDS-1,5-2-5.08_1x02_P5.08mm_Horizont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
J2, J3, J4, J5: Conn_01x03_Pin; PinHeader_1x03_P2.54mm_Vertical
Peltier1: MOSFET_KIT
U1: ESP32-S3-DEVKITC-1-N8R2; XCVR_ESP32-S3-DEVKITC-1-N8R2
Waterpump1, Waterpump2: MOSFET_KIT
peltier2: MOSFET_KIT

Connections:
Dht22: J4.2, U1.J1_4 (GPIO4)
Fan: Fan1.2 (PMW), U1.J1_9 (GPIO16)
GND: Fan1.1 (GND), Heatlamp1.1 (GND), Humidifer1.1 (GND), J1.2, J2.3, J3.1, J4.1, J5.2, Peltier1.1 (GND), U1.J1_22 (GND), U1.J3_1 (GND), U1.J3_21 (GND), U1.J3_22 (GND), Waterpump1.1 (GND), Waterpump2.1 (GND), peltier2.1 (GND)
Heatlamp: Heatlamp1.2 (PMW), U1.J1_16 (GPIO10)
Humidifier: Humidifer1.2 (PMW), U1.J1_18 (GPIO12)
LDR: J5.1, U1.J3_5 (GPIO2)
Peltier1: Peltier1.2 (PMW), U1.J1_6 (GPIO6)
Peltier2: U1.J1_12 (GPIO8), peltier2.2 (PMW)
Soil: J3.3, U1.J3_14 (GPIO0)
VCC: J1.1, J2.2, J3.2, U1.J1_21 (5V0)
VCC_3v: J4.3, J5.3, U1.J1_1 (3V3), U1.J1_2 (3V3)
Water_level: J2.1, U1.J1_11 (GPIO18)
Waterpump: U1.J1_20 (GPIO14), Waterpump1.2 (PMW)
grow: U1.J3_13 (GPIO35), Waterpump2.2 (PMW)

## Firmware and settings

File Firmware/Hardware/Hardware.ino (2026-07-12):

// libraries importing
#include "DHT.h"
#include <WiFi.h>
#include <Firebase_ESP_Client.h>
#include "addons/TokenHelper.h"
#include "addons/RTDBHelper.h"

// firebase realtime
#define WIFI_SSID "***********"
#define WIFI_PASSWORD "*************"
#define FIREBASE_URL "https://console.firebase.google.com/project/clas-59589/database/clas-59589-default-rtdb/data"
#define FIREBASE_SECRET "**************"

// sensors definition
#define DHTPIN 4
#define DHTTYPE DHT22
#define LDR_pin 2
#define Soil_pin 0
#define water_level_pin 18

// power controllers definition
#define peltier1 6
#define peltier2 8
#define heatlamp 10
#define Humidifier 12
#define waterpump 14
#define fan_h 16
#define growlight 35
// var ranges
struct ranges
{
  int templow;
  int temphigh;
  int humidlow;
  int humidhigh;
  int soillow;
  int soilhigh;
  int lightlow;
  int lighthigh;
}
// lettuce
const ranges lettuce = {
    15, 24,
    60, 80,
    2100, 1400,
    1500, 700};
// pepper
const ranges pepper = {
    20, 30,
    55, 75,
    2100, 1400,
    1500, 700};

DHT dht(DHTPIN, DHTTYPE);
// firebase
FirebaseData fbdo;
FirebaseAuth auth;
FirebaseConfig config;
unsigned long sendDataPrevMillis = 0;
// status actuctors
int pel1 = 0, pel2 = 0, fan = 0, lamp = 0, light = 0, humid = 0, pump = 0;
void setup()
{
  Serial.begin(115200);
  dht.begin();
  pinMode(LDR_pin, INPUT);
  pinMode(Soil_pin, INPUT);
  PinMode(water_level_pin, INPUT);
  PinMode(peltier1, OUTPUT);
  PinMode(peltier2, OUTPUT);
  PinMode(heatlamp, OUTPUT);
  pinMode(Humidifier, OUTPUT);
  pinMode(waterpump, OUTPUT);
  pinMode(fan_h, OUTPUT);
  pinMode(growlight, OUTPUT);
  // wifi connection
  Wifi.begin(WIFI_SSID, WIFI_PASSWORD);
  while (WiFi.status() != WL_CONNECTED)
  {
    delay(300);
    Serial.print(".");
  }
  config.database_url = FIREBASE_URL;
  config.signer.tokens.legacy_token = FIREBASE_SECRET;
  Firebase.begin(&config, &auth);
  Firebase.reconnectWiFi(true);
  delay(5000);
}

void loop()
{
  // plant type
  int planttype = 0;
  if (Firebase.RTDB.getInt(&fbdo, "/greenhouse/plant_type"))
  {
      planttype = fbdo.intData();
  }
  double temperature = dht.readTemperature();
  double Humidty = dht.readHumidty();
  int light = analogRead(LDR_pin);
  float soilmoisture = analogRead(Soil_pin);
  int waterlevel = analogRead(water_level_pin);
  float waterprecent = (waterlevel / 4095.0) * 100;

  serial.print("Temperature :")
  serial.print(temperature);
  serial.print("Celsuis / Humidty : ");
  serial.print(" % / Soil Moisture : ");
  serial.print(soilmoisture);
  serial.print(" % / Light Amount : ");
  serial.print(light);
  serial.print(" % / Water level : ");
  serial.print(waterlevel);
  serial.print(" % ");
  if (planttype == 0)
  {
    // temperature
    if (temperature > lettuce.temphigh)
    {
      analogWrite(peltier1, 255);
      analogWrite(peltier2, 255);
      analogWrite(heatlamp, 0);
      pel1 = 1, pel 2 = 1, lamp = 0;
    }
    else if (temperature < lettuce.templow)
    {
      analogWrite(peltier1, 0);
      analogWrite(peltier2, 0);
      analogWrite(heatlamp, 255);
      pel1 = 0, pel 2 = 0, lamp = 1;
    }
    else
    {
      analogWrite(peltier1, 0);
      analogWrite(peltier2, 0);
      analogWrite(heatlamp, 0);
      pel1 = 0, pel 2 = 0, lamp = 0;
    }
    // Humidty
    if (Humidty > lettuce.humidhigh)
    {
      analogWrite(Humidifier, 0);
      analogWrite(fan, 255);
      humid = 0, fan = 1;
    }
    else if (Humidty < lettuce.humidlow)
    {
      analogWrite(fan, 0);
      analogWrite(Humidifier, 255);
      humid = 1, fan = 0;
    }
    else
    {
      analogWrite(fan, 0);
      analogWrite(Humidifier, 0);
      humid = 0, fan = 0;
    }
    // Soil
    if (soilmoisture > lettuce.soilhigh)
    {
      analogWrite(waterpump, 0);
      pump = 0;
    }
    else if (temperature < lettuce.soillow)
    {
      analogWrite(waterpump, 255);
      pump = 1;
    }
    else
    {
      analogWrite(waterpump, 0);
      pump = 0;
    }
    // Light
    if (light > lettuce.lighthigh)
    {
      analogWrite(growlight, 255);
      light = 1;
    }
    else if (light < lettuce.lightlow)
    {
      analogWrite(growlight, 0);
      light = 0;
    }
    else
    {
      analogWrite(growlight, 0);
      light = 0;
    }
  }
  else if (planttype == 1)
  {
    // temperature
    if (temperature > pepper.temphigh)
    {
      analogWrite(peltier1, 255);
      analogWrite(peltier2, 255);
      analogWrite(heatlamp, 0);
      pel1 = 1, pel 2 = 1, lamp = 0;
    }
    else if (temperature < pepper.templow)
    {
      analogWrite(peltier1, 0);
      analogWrite(peltier2, 0);
      analogWrite(heatlamp, 255);
      pel1 = 0, pel 2 = 0, lamp = 0;
    }
    else
    {
      analogWrite(peltier1, 0);
      analogWrite(peltier2, 0);
      analogWrite(heatlamp, 0);
      pel1 = 0, pel 2 = 0, lamp = 0;
    }
    // Humidty
    if (Humidty > pepper.humidhigh)
    {
      analogWrite(Humidifier, 0);
      analogWrite(fan, 255);
      humid = 0, fan = 1;
    }
    else if (Humidty < pepper.humidlow)
    {
      analogWrite(fan, 0);
      analogWrite(Humidifier, 255);
      humid = 1, fan = 0;
    }
    else
    {
      analogWrite(fan, 0);
      analogWrite(Humidifier, 0);
      humid = 0, fan = 0;
    }
    // Soil
    if (soilmoisture > pepper.soilhigh)
    {
      analogWrite(waterpump, 0);
      pump = 0;
    }
    else if (temperature < pepper.soillow)
    {
      analogWrite(waterpump, 255);
      pump = 1;
    }
    else
    {
      analogWrite(waterpump, 0);
      pump = 0;
    }
    // Light
    if (light > pepper.lighthigh)
    {
      analogWrite(growlight, 255);
      light = 1;
    }
    else if (light < pepper.lightlow)
    {
      analogWrite(growlight, 0);
      light = 0;
    }
    else
    {
      analogWrite(growlight, 0);
      light = 0;
    }
  }
  else
  {
    // manual mode
    String controlBase = "/gardenConfig/actuators/";
    if (Firebase.RTDB.getBool(&fbdo, controlBase + "peltier1"))
      analogWrite(peltier1, fbdo.boolData() ? 255 : 0);
    if (Firebase.RTDB.getBool(&fbdo, controlBase + "peltier2"))
      analogWrite(peltier2, fbdo.boolData() ? 255 : 0);
    if (Firebase.RTDB.getBool(&fbdo, controlBase + "heatlamp"))
      analogWrite(heatlamp, fbdo.boolData() ? 255 : 0);
    if (Firebase.RTDB.getBool(&fbdo, controlBase + "humidifier"))
      analogWrite(humidifier, fbdo.boolData() ? 255 : 0);
    if (Firebase.RTDB.getBool(&fbdo, controlBase + "waterpump"))
      analogWrite(waterpump, fbdo.boolData() ? 255 : 0);
    if (Firebase.RTDB.getBool(&fbdo, controlBase + "fan"))
      analogWrite(fan, fbdo.boolData() ? 255 : 0);
    if (Firebase.RTDB.getBool(&fbdo, controlBase + "growlight"))
      analogWrite(growlight, fbdo.boolData() ? 255 : 0);
  }
  // update firebase
  FirebaseJson updateData;
  updateData.set("sensors/temperature", temperature);
  updateData.set("sensors/humidity", humidity);
  updateData.set("sensors/light", light);
  updateData.set("sensors/soil_moisture", soilmoisture);
  updateData.set("sensors/water_level", waterlevel);
  updateData.set("sensors/water_percent", waterpercent);

  if (planttype != 3)
  {
    updateData.set("actuators/peltier1", pel1);
    updateData.set("actuators/peltier2", pel2);
    updateData.set("actuators/heatlamp", lamp);
    updateData.set("actuators/humidifier", humid);
    updateData.set("actuators/waterpump", pump);
    updateData.set("actuators/fan", fan);
    updateData.set("actuators/growlight", light);
  }
  if (Firebase.RTDB.updateNode(&fbdo, "/greenhouse", &updateData))
  {
    Serial.println("Firebase updated successfully.");
  }
  else
  {
    Serial.println("Firebase update failed: " + fbdo.errorReason());
  }

  delay(30000);
}
